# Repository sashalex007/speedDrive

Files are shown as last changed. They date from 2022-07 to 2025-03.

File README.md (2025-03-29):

# SpeedDrive documentation 

Update: Moving this project to github. Future updates will be here. Included step file.

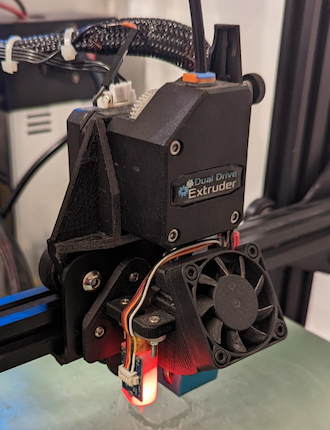
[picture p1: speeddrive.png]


The motivation behind creating the SpeedDrive mount was to extract maximum performance out of my ender3 with mostly stock parts. Print FAST with near-perfect quality. After pushing Bowden to its limit, I came to the conclusion (like many others), that sharp and accurate corners are simply impossible with a Bowden setup. Bowden setups are great for models with curvature, but for my particular uses, I was printing precisely engineered parts that often needed to fit together. Bowden setups produce poor corners because of imprecise linear/pressure advance due to play and friction inside the Bowden tube. This can be reduced to some extent, but never entirely eliminated.

I started playing around with various mount designs and found them to be inadequate. The corners were good, but ringing and vibration prevented high speed printing and good bed adhesion. The orientation of the motor and distance from the X extrusion was not suited for sufficient inertial dampening.  

In creating this mount, there were two operating principles:

1. Orientation of the motor (shaft) should be perpendicular to the X extrusion for good absorption of rotational inertia. 

2. The motor's centre of mass should be as close as possible to the middle of the X extrusion for absorption of its significant linear inertia at speed. 

Staying true to the operating principles, my solution was to mount the motor from behind the carriage with the extruder facing forwards. Speeds upwards of 100mm/s and accelerations of 3000+ are not only possible, these are real operating speeds that I have been using day to day for all my prints (see image of [xyz cube](https://imgur.com/zxmh5d8)). By no means is your printer guaranteed to get these results right off the bat, start at 1500accel and work up from there. 

There are now several designs and remixes claiming to be an improvement over the original SpeedDrive. I am all for innovation, however many of these designs violate one or both of the operating principles inherent to the SpeedDrive design. For this reason, I would not recommend any design or remix not explicitly listed on this page. Remixes and improvements are welcome however I encourage designers to stay faithful to the design principles. 

## IMPORTANT NOTE!!

The only downside to this solution is that the stock motor will slam into the frame unless the X endstop is adjusted. Therefore, I have also designed a 7.5mm endstop spacer that fits onto the carriage. This will shorten the bed in the X orientation by roughly 1cm on each side. In slicer, your Ender's bed size should also be changed to 200mm in the X direction.

See the [remix by dascook](https://www.thingiverse.com/thing:3990436) for reclaiming lost X space if thats important to you (BMG only, pancake stepper required).

Also, for very tall prints you will need to extend the e-motor cable and adjust the printer's Z height in slicer to 200mm. 

## DEMO

This is a demo of a near-perfect calibration cube printed in 13minutes using Klipper firmware and pressure advance (see [picture](https://imgur.com/zxmh5d8)). When my ender was still Bowden, I could only manage a 15minute cube with acceptable results. I don't know what to make of this because in theory, the Bowden setup should get higher speeds but it appears that superior corner performance and placement of the SpeedDrive negates the weight disadvantage. This is actually not that surprising because PRUSA printers are known to print at these speeds with similar quality. 

IMAGE ALT TEXT (http://www.youtube.com/watch?v=PnwfLujIF-U "Video Title")

## SPEEDDRIVE PRINT AND INSTALLATION

Print with the [flat part down](https://imgur.com/Yqz5DUt), at least 4 walls and 50% gyroid infill. Enable support roof. 0.2 should be fine. PLA is fine. 

I recommend tightening the mount first without the v-wheel sleeves. This will "set" the middle hole and close that gap with the carriage. 

The sleeves will be very tough to fit into the mount holes, but should eventually go in with enough force. This is by design because these are the only points holding the mount. One user reported easier installation by heating the sleeves with soldering iron prior to installation. 

See comments section for more installation tips.

Also see this great installation video by [YouMakeTech](https://www.thingiverse.com/youmaketech/designs) \
https://www.youtube.com/embed/Zbk0viFC1ew

## COOLING

### UPDATE 2022
I have since removed all part cooling from my setup because I now only print with nylon and polycarbonate. Part cooling is undesirable for these materials. In light of this, I have designed a new cooling base (based on herome design) with an integrated BLtouch mount. This is the setup shown in the top image. See the following file:  \
[`speedDrive_heromeBase_bltouch_combined.stl`](./STL/speedDrive_heromeBase_bltouch_combined.stl)

### Stock 4010
Cooling at these speeds becomes an issue. Staying true to stock parts, my goal was to squeeze the most cooling performance out of the 4010 blower. I was was very disappointed with the Hero Me because I really liked the compact design. There are some who feel that it's equal to the bullseye, but I have not seen tests at these kinds of speeds. I found the Hero Me's cooling to be too asymmetrical and lacking correct directionality due to the duct design. The designer of the hero me himself was reluctant to adapt his design to the 4010 cooler, and only did so as a user request. 

The bullseye on the other hand provides adequate cooling, and I've yet to see its limits. The only downside to the bullseye is that the orientation of the fan causes a bit of a rattle inside the sleeve bearing. A bit of lubrication can temporarily alleviate this but so far I have not found a permanent solution. Either way, I have seen no evidence that the rattle impacts print quality whatsoever. 

I have included a slightly modified bullseye base for compatibility with SpeedDrive mount and endstop spacer. SpeedDrive is also fully compatible with the stock cooler.  

### Dual 5015
I really like the hero me dual fan design with the light-weight dual ducts (see image of my BMG setup). I have also included a slightly modified hero me base for compatibility with the SpeedDrive. Dual 5015 fans will absolutely cause clogging if installed incorrectly. Make sure they are blowing on the print, not the nozzle.

### NOTE
Both herome and bullseye have a fairly flimsy mounting system for the ducts. I just epoxied the ducts to the base for improved fidelity. 

## TL SMOOTHERS

NOTE: This section does not apply to TMC drivers. TL smoother will certainly not be needed with most modern 32bit boards. I wrote this section with the stock ender3 board in mind.  

There seems to be some debate over whether or not TL smoothers are necessary on an ender3. I believe the source of this debate is actually due to the fact that the play and springiness of the filament inside the Bowden tube absorbs the voltage spikes of the extruder motor and evens out the extrusion. Using the SpeedDrive however, the filament flow is much more precise, so artifacts are readily visible (please see [image](https://imgur.com/Q9a78i5)). 

In my opinion, TL smoothers are not strictly necessary with the SpeedDrive, however using them will yield significant improvements in surface quality. Priority should be placed on the extruder motor, with X and Y smoothers yielding modest improvements, and no visible improvements on the Z motor. 

## KLIPPER FIRMWARE

HIGHLY recommend klipper firmware. If you want to get the most out of the speedDrive, strongly consider upgrading to Klipper. This firmware is at least as effective as the speedDrive itself (likely more so) for boosting speeds while maintaining quality. 

See my speed/quality [comparisons](https://i.imgur.com/cMr6vmC.jpg) (compared on my old Bowden setup)

[Get started with klipper](https://www.klipper3d.org)

NOTE: I run klipper firmware and octoprint off a rooted Nexus 7 tablet. I co-authored [this installation guide](https://community.octoprint.org/t/assorted-guides-as-formerly-maintained-on-the-github-wiki/21146) for octoprint on android devices. If you are interested in how this is accomplished, or would like to run klipper+octoprint off an android device please check out the guide. 

## GLASS BED OR STOCK?

Unless your bed is warped, a glass bed will do more harm than good. The extra weight of the glass bed will cause significantly more ringing at high speeds. It's also not nearly as sticky as the stock surface, and high speed prints are more likely to come loose due to inertia. Avoid the glass bed if you can.

## NOZZLE

I have found that the quality of nozzle is a very important consideration. The stock creality nozzle is quite good and there is no need to change it for cheap amazon nozzles. Those cheap nozzles will ruin surface quality and reduce the effectiveness of your linear/pressure advance. Make sure you purchase your nozzles from a reputable source...amazon reviews are worthless here.

## RECOMMENDED UPGRADES

1. Klipper firmware
2. Yellow springs
3. Z motor spacer 
4. Z rod stabilizer
5. [X belt tensioner](https://www.thingiverse.com/thing:2854971)
6. Bullseye with modified base (provided) [or any 5015 cooling]
7. TL smoothers (e,x,y) [not for TMC drivers]

## THOUGHTS ON GENERAL ASSEMBLY 

I have seen conflicting opinions on how to assemble your ender 3. The consensus seems to be "tight but not too tight". I somewhat disagree with this. Loose parts are just quick fixes for underlying alignment issues. Everything on my printer, from the belts to the bolts, are very tight apart from the V wheels and eccentric nuts. 

## THOUGHTS ON VARIOUS OTHER UPGRADES

### SKR 1.3
I upgraded to an skr 1.3+TMC2209's in hopes of even better quality. I only saw a very slight improvement in surface quality, speed remained the same. Note that this is with klipper firmware, I cannot speak to improvements with marlin. 

### BMG extruder(trianglelab)
Significant improvements in surface quality over the stock extruder, only noticeable under acute light.

### V6 hotend
It works well enough, but its position further out from the carriage throws the balance out of whack. Also you can't bolt it on like a micro-swiss/stock so there isn't perfect connection with the carriage; this becomes apparent at high accelerations. All this said, see the excellent [remix by Foxburrow](https://www.thingiverse.com/thing:3996864) if you are still intent on using the V6.

### Microswiss(trianglelab)
Nice upgrade for higher temp filaments, however, does not improve PLA performance. 

### Dual 5015 fans
Nice upgrade, significant improvement in cooling performance over the bullseye. Its worth mentioning that if your goal is to print higher temp filaments like nylon and PETG for functional parts, you will want to turn off your cooling completely for maximum part strength. If this is your goal, I wouldn't bother with this upgrade. 

Note: After having the dual fans for some months, I now believe that this is an overkill upgrade that causes more problems than it solves. Going back to single 5015.

### Bltouch/3dtouch
Pretty nice upgrade, but it's important to mention that it has a couple limitations. 1. It won't work properly unless the bed is already level; even a 2mm deviation will throw it off. 2. It does not compensate for gantry slop, which is present on every creality style printer; I will be upgrading in the near future to belt driven dual z screw. Either way, if your bed is not warped, this is just a glorified endstop. There is some extra utility though if you constantly swap build surfaces. 

## FILES YOU NEED

### Stock extruder (no cable links)
[`speedDrive_mount.stl`](./STL/speedDrive_mount.stl) \
[`speedDrive_endstop.stl`](./STL/speedDrive_endstop.stl)

### Stock extruder (cable links version A)
[`speedDrive_mount_cableClip.stl`](./STL/speedDrive_mount_cableClip.stl) \
[`speedDrive_endstop.stl`](./STL/speedDrive_endstop.stl) \
https://www.thingiverse.com/thing:3475424

### BMG extruder (no cable links)
[`speedDrive_mount_bmg.stl`](./STL/speedDrive_mount_bmg.stl) \
[`speedDrive_endstop_bmg.stl`](./STL/speedDrive_endstop_bmg.stl)

### BMG extruder (cable links version A)
[`speedDrive_mount_bmg_cableClip.stl`](./STL/speedDrive_mount_bmg_cableClip.stl) \
[`speedDrive_endstop_bmg.stl`](./STL/speedDrive_endstop_bmg.stl) \
https://www.thingiverse.com/thing:3475424

### CR-10s PRO extruder
[Remix by fsironman](https://www.thingiverse.com/thing:3956497) \
[`speedDrive_endstop.stl`](./STL/speedDrive_endstop.stl)

### Redrex geared extruder
[Remix by huubert](https://www.thingiverse.com/thing:4159487)

### Ender 5 - stock extruder
[Remix by paydayxray](https://www.thingiverse.com/thing:4310609)

### Ender 5 - BMG
[Remix by stijoh](https://www.thingiverse.com/thing:4348063)

### Geeetech A10 -- BMG/Stock
[Remix by Cyg0r3](https://www.thingiverse.com/thing:4335703)

### OPTIONAL MODS
[Pi camera mount by elcojacobs](https://www.thingiverse.com/thing:3965589)
[Clever X-cover with endstop by R3br0d0n](https://www.thingiverse.com/thing:4068615) (BMG only)

## STEP FILES FOR DESIGNERS
[`speedDrive_stepFile.step`](./speedDrive_stepFile.step)

## CREDITS 

Design for V-wheel mount is from [here](https://www.thingiverse.com/thing:3369418) \
Bullseye ducts can be found [here](https://www.thingiverse.com/thing:2759439) \
Hero Me ducts [here](https://www.thingiverse.com/thing:3182917) \
Special thanks to u/TianZiGaming for educating me on direct drive setups. \
Thanks to u/ColonelMu5t4rd for beta testing the BMG version. \
Thanks to [fsironman](https://www.thingiverse.com/fsironman/about) for the remix supporting the CR-10s PRO extruder. \
Thanks to [huubert](https://www.thingiverse.com/huubert) for the remix supporting the Redrex extruder \
Thanks to [paydayxray](https://www.thingiverse.com/paydayxray/about) for the remix supporting the ender 5 \
Thanks to [stijoh](https://www.thingiverse.com/thing:4348063) for the remix supporting BMG extruder for the ender 5 \
Thanks to to [Cyg0r3](https://www.thingiverse.com/Cyg0r3/about) for the remix supporting the Geeetech A10 \
Thanks to to [Garigen](https://www.thingiverse.com/garigm/designs) for the remix supporting the EZR Struder \
Thanks to [YouMakeTech](https://www.thingiverse.com/youmaketech/designs) for the great installation video

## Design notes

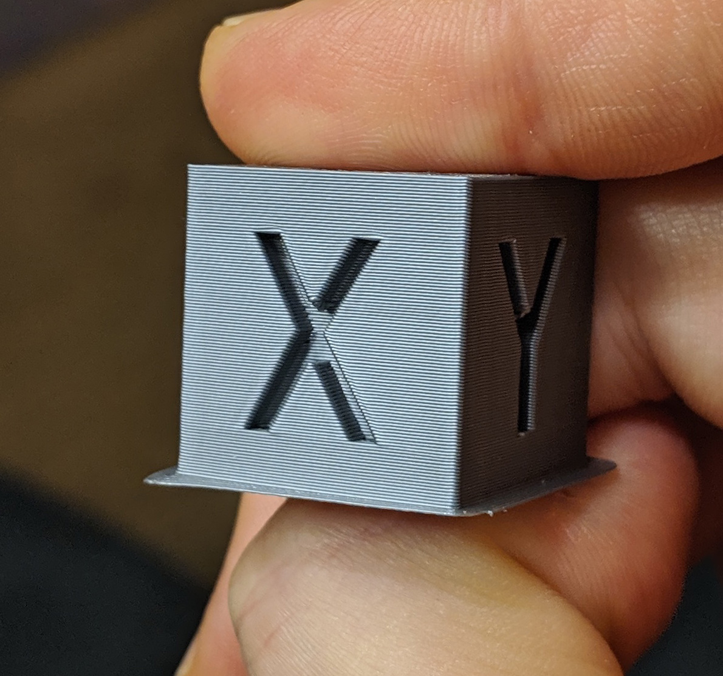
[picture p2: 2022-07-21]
xyz.jpeg

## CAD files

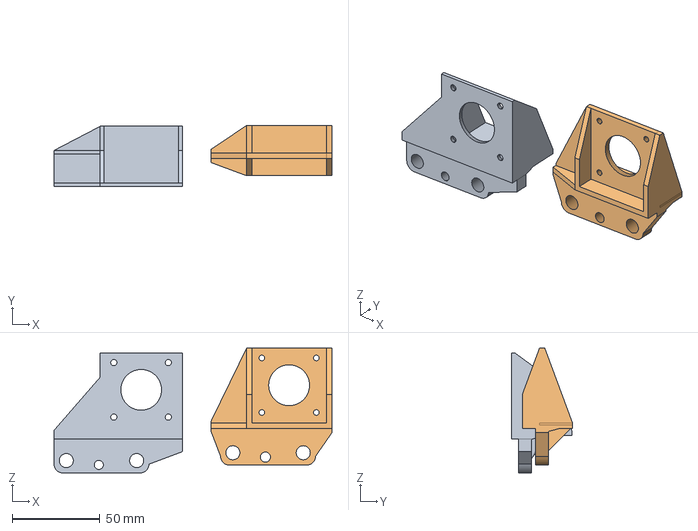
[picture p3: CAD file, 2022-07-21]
speedDrive_stepFile.step
158.1 x 34.8 x 71.0 mm
speedDrive_stock
bmg

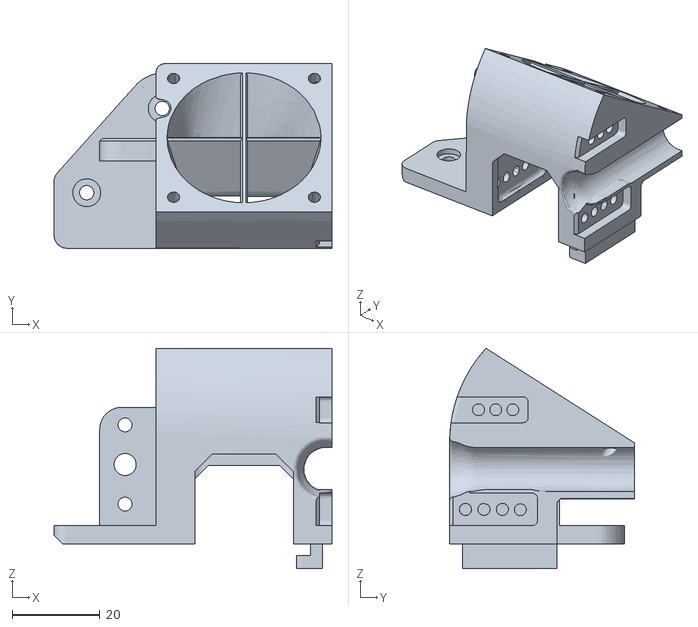
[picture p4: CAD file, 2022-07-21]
STL/speedDrive_heromeBase_bltouch_combined.stl
63.2 x 42.0 x 50.1

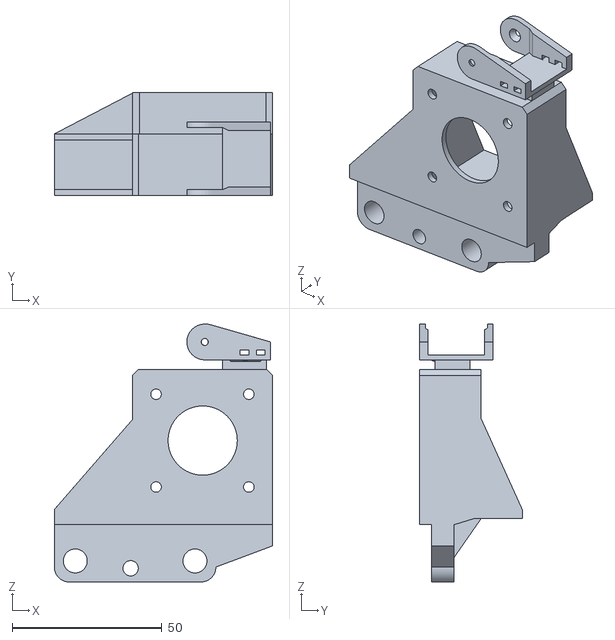
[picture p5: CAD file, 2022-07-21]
STL/speedDrive_mount_cableClip.stl
73.0 x 34.4 x 86.2

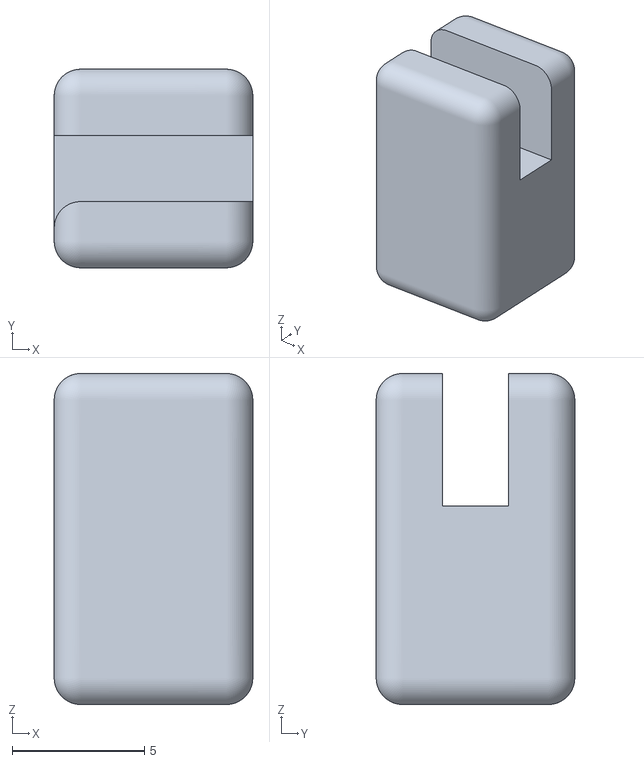
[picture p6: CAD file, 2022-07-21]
STL/speedDrive_endstop.stl
7.50 x 7.50 x 12.5

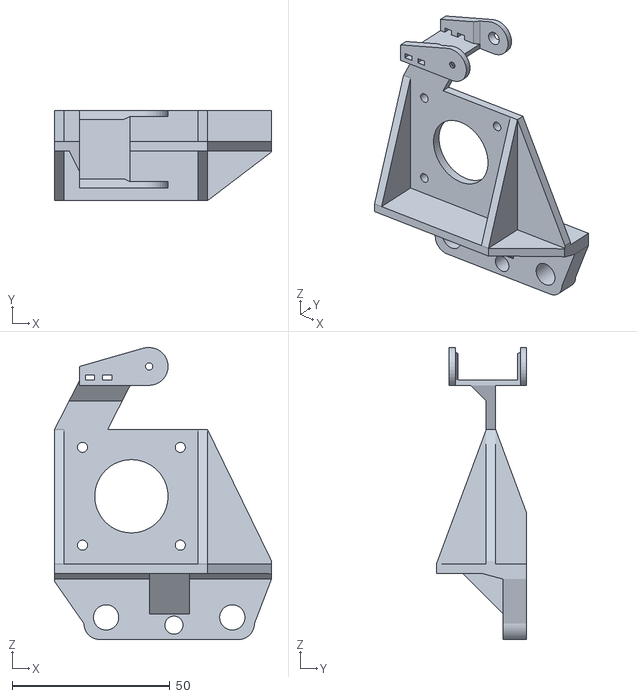
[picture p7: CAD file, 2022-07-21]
STL/speedDrive_mount_bmg_cableClip.stl
68.8 x 28.6 x 92.5

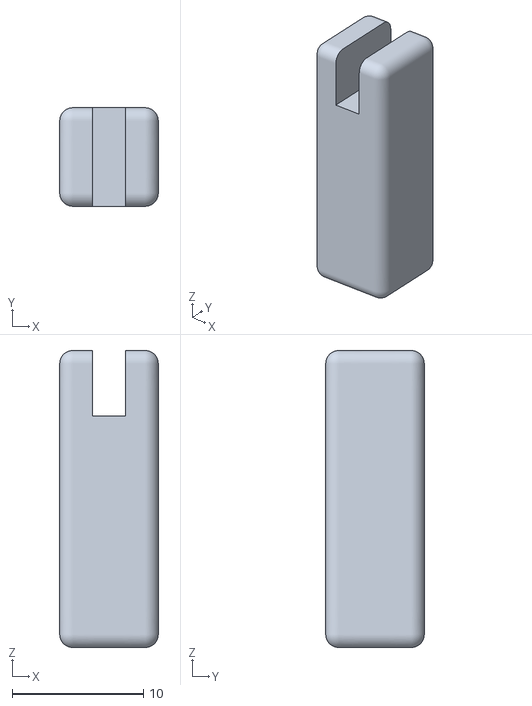
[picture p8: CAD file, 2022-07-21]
STL/speedDrive_endstop_bmg.stl
7.50 x 7.50 x 22.6

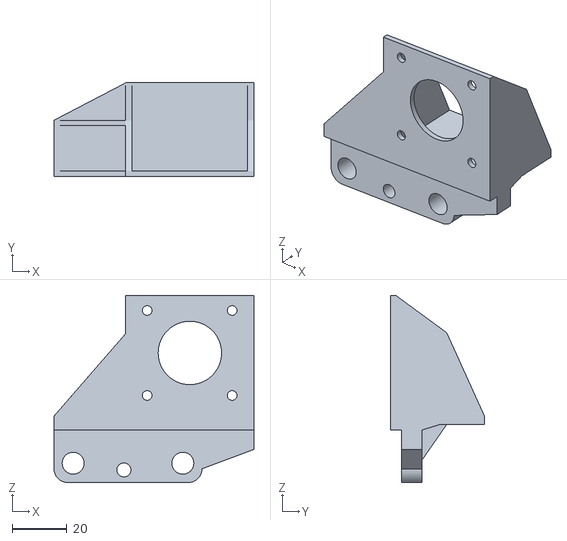
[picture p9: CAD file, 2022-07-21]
STL/speedDrive_mount.stl
73.0 x 34.4 x 68.2

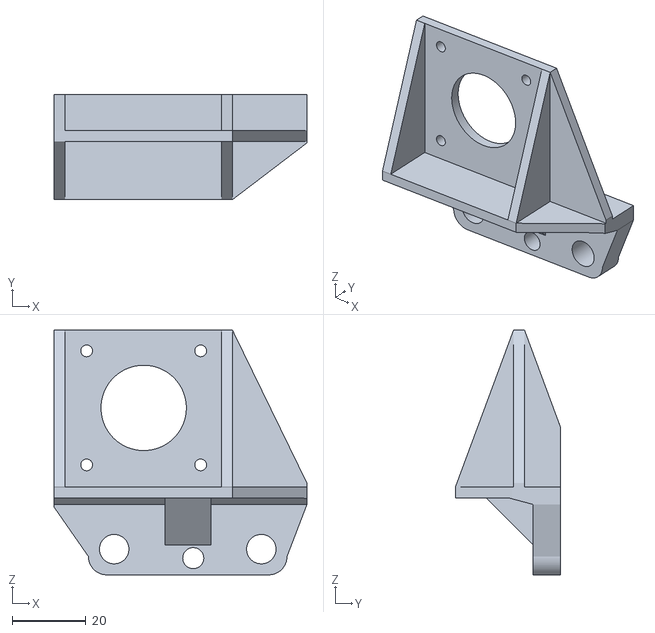
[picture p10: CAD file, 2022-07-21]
STL/speedDrive_mount_bmg.stl
68.8 x 28.6 x 66.5

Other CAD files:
STL/speedDrive_heromeBase.stl

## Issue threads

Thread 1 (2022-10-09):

Klipper Config and Slicer Settings

zimmra, 2022-10-09:
Hoping to get a bit more insight on specific acceleration levels and speeds you've had success with in your Klipper config and your slicer settings.

Are the default Klipper settings for the Ender 3 okay to leave as is?

```
[printer]
kinematics: cartesian
max_velocity: 300
max_accel: 3000
max_z_velocity: 5
max_z_accel: 100
```

You mentioned 100mm/s and 1000mm/s<sup>2</sup> acceleration. Are you just doing that flat across the board, or are you tweaking it for outer layers/first layer/etc?

The files themselves printed as intended and all seems to fit just fine, now just looking to dial in the software.

sashalex007, 2022-10-09:
Those settings look OK. TBH, I have not yet messed around with newer versions of klipper so you can consider my knowledge out of date. At the time that speed drive was created, the speeds I was running were almost unheard of for ender 3. Now with input shaping and other features I think speeds and accelerations can be pushed alot higher with no loss in quality. I would check out the klipper discord for expert software tuning.

Closed 2022-10-09.

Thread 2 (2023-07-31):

Speeddrive with Micro-Swiss all hetal hotend + cr-touch ?

lavinir, 2023-07-31:
Hi,

Thank you so much for this project! I'm trying to figure out whether this would be compatible with my current setup - Ender 3 with an upgraded Creality all metal extruder and a Micro-Swiss all metal hotend with a CR-touch.
My main concerns are
* Would the Micro-Swiss hotend fit well ?
* Can I still use my CR-touch. (I saw there is the herobase with bltouch-  possibly that would work?) Are the bases something that needs to be attached to the mount or are they a replacement for the mount alltogether ?

Really appreciate the help!

Closed 2023-08-10.

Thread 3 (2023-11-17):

What hardware do you use in your attached picture

BamiPen, 2023-11-17:
Hi,

This looks like a very nice project!!

I see that you have an pancake stepper setup yourself displayed in the attaced picture.

Coud you share your used hardware?
Whicht stepper did you use and what are your Vref settings for this stepper?
Do you have full bed and heigth available in the option in the picture?

Kind regards,

Thijs

sashalex007, 2025-03-29:
Sorry for the late reply. This is a 20mm stepper and I think the vref is 0.6-0.8, and yes I have access to the full bed with this setup

Closed 2025-03-29.

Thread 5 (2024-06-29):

fan mount for speed drive with BLTOUCH

Leygan1, 2024-06-29:
hello, i am using speedDrive_heromeBase_bltouch_combined.stl

What fan can I add for part cooling? I have problems with printing without fan :(

Leygan1, 2024-07-13:
nothing?

sashalex007, 2024-07-13:
Sorry for the late reply. I use [this duct](https://www.thingiverse.com/thing:3779498/files), on the right side.

Closed 2024-07-13.

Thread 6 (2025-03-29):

Zero clearance high friction v wheels

ricosolana, 2025-03-29:
Hi,

The clearance between the two top x roller wheels and the printed mount is too small. The wheels do not roll depending on deep the stock spacers are pushed into the printed mount holes. It is very easy to mess up this micro alignment when pushing in the spacers, and a huge hassle to push it back the other direction.

I did not tighten the nuts to the expected amount. Loosening the nuts enough to allow for wheel rotation results in the entire assembly being very loose.

I figure a solution would be to have two 24mm diameter cutouts around each of the roller wheel holes placed into the mount. Somewhere between a cut height of 0.4mm and 1.0mm should be fine (likely 0.8mm).

Then add a minor extruded spacer on the roller wheel side that will extend outwards (increasing radius/diameter) until it just almost touches the outer bearing of the roller wheel.

I created a remix below: I still have yet to print and test this remix, but will soon.

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

https://www.tinkercad.com/things/jY0ACc9LUQA-speeddrive-wheel-clearance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

sashalex007, 2025-03-29:
Thanks for sharing. Let me know how it goes. If it works well I'd consider merging it.

ricosolana, 2025-03-29:
So the wheels do turn now, but there is an issue with the wheel-side plastic ring spacer. Its too thin, so it was torn when fitting the stock spacer on.

I did try heat-setting the stock spacer into place for a more snug fit. But when I tightened the bolt back on, it slid... The same problem is being caused as before, plus its misaligned with the opposite spacer, angling the entire mount.

left spacer is intact (good gap between printed mount and roller wheel):
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

right is bad (gap between metal and printed mount):
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

Maybe the rings can be expanded, but not sure how much more before it causes friction issues again. The rings could be beveled like the outer cutout to avoid being easily torn during install.

The best solution would to use metal rings with inner diameter a bit larger than 8mm and an outer diameter around 8.8mm (ideally should be larger than the stock spacer to avoid going back into the hole). But this seems extra... Maybe some bread ties or other wire would fit fine. They can be tightly wrapped around like twice without causing major issues. As far as I can tell, I don't think inserting a wire spacer like this would come with any problems later, these parts do not move since its only the bearing moving.

ricosolana, 2025-03-30:
I decided to remove the carriage from the gantry so inspect things.

I was wondering regardless of what I changed, why was the mount always being offset/pushed away from the metal carriage. I found that the middle fan screw had a lip on the wheel side. There is a hole in the speedMount to account for this, but I guess mine printed out very tightly.

I don't think this hole requires a press fit, because of how shallow the protrusion is; there is not much for the hole to grab onto to ensure a secure press fit. This just results in the funky problem I was having:
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

I propose maybe increasing the diameter of this hole by at least 0.2mm to ensure a mild-loose fit.

Regarding the ring spacer, I have a solution, which might apply to anyone who wants to use it. I had some crappy solder from Aliexpress that ended up being high tin %. I decided to use this because it was the only thick wire I had. I pushed up a little on the spacer that was press fit into the speedMount to use as a wraparound for the wire. I made a little ring with the tin. I then got my soldering iron to join the ends of the ring. I put the iron to 450c (max), tipped the iron with some of the tin, then very quickly tapped the ends of the wire to join them, see below:
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

I made a total of two rings, but lost the other one. The one shown is the crappier one which I guess came out a little pancaked on the join. I didn't really get a chance to test this ring out on the mount because of the middle hole problem, but will return when I find out something new.

ricosolana, 2025-03-30:
I lost one of my screws...

Anyways, I see that the protruded screw hole can have a nut put on the other side to batter secure it against the gantry?

This might completely overwrite the need for funky spacers. Only the hole might need to be smaller further along the hole for better securing a nut. But still bevel it closer to the gantry side to fit the protrusion. I'll model a sketch.

ricosolana, 2025-03-30:
This is the new design:
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

I removed the plastic rings, raised the wheel cutout 0.5mm (because no need for rings), decreased the diameter of the middle shroud fan hole (for the M3 screw).

I also added a cone cutout opposite to the wheel side for the protrusion:
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

To best secure the speedMount, maybe use an M3 nut (or nyloc) on the other end of the middle fan shroud hole. The only thing is that a longer M3 would be needed here. This nut is hard to reach, so it might be best to use a proper socket instead of the flat wrenches.

Its important to note that I have not tested or printed the revisions above. Theoretically, they should work. I feel like I have done enough testing, disassembling and reassembling of my print head several times.

Closed 2025-03-31.
